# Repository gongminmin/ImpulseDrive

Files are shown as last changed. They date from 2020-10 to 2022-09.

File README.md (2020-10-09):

# Impulse Drive



In Star Trek universe, impulse drive is a propulsion system of spacecrafts for interplanetary travel. This project is trying to design a real-world impulse drive. The basic characteristics of this engine are

* Electric propulsion
* Large thrust
* Long specific impulse
* No or little moving parts
* Good scalability
* Low cost

We'd like to make it easy to implement, so people can build it as a hobby project.

NOTE: Please turn on git LFS when cloning this project.

## Method

There are many different engine designs for spacecraft propulsion, check [wikipedia](https://en.wikipedia.org/wiki/Spacecraft_propulsion#Table_of_methods) for a list. The only one design among them that fits these requirements is magnetoplasmadynamic thruster, a.k.a, MPDT or MPD thruster. More details in [MPD](Doc/Mpd.md).

Our design is based on MPDT, with several significant improvements.

## Design

The principle of our design, and a detailed introduction of modules are in [Design](Doc/Design.md)

## Disclaimer

MPD thruster is operated by **LETHALLY** high voltage and current. If you don't have enough knowledge and experiences on high voltage electric, please keep extreme cautions on insulation.

## Directories

* Circuit folder is the electric design of the system. The files can be open by [KiCad](https://kicad-pcb.org/)
* 3DModel folder is the 3D model design of some components. It's in [Blender](https://www.blender.org/) format.
* Doc folder contains some documents

## License

ImpulseDrive is distributed under the terms of MIT License. See [LICENSE](LICENSE) for details.

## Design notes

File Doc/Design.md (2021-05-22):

# Design

To make MPD thruster practical enough, we need to solve [drawbacks of MPD thruster](Mpd.md#Drawbacks).

## Improvements

### Power Source

To ionize the propellant, the power voltage needs to be very high. To generate large enough Lorentz force, the electric current need to be very high. However, a power source with both high voltage and high current is not practical.

To solve this, we borrow a concept from a welding machine. In its design, a starter provides 10kV high frequency AC to ionize some of the medium particles. An ion path is created from one electrode to another during the ionization phase. This path closes a low voltage capacitor bank circuit, which then pumps a high current to the medium to generate much more ion. One bonus is that AC is much easier to ionize medium than DC, it reduces the voltage requirement of the starter.

In this way, we need a power source to provide high voltage and low current, and a power source to provide high current and low voltage. The power requirement is reduced much.

### Parallel or Series

Now we have 2 power sources, one high voltage AC from starter and one high current DC from capacitor bank. But how to connect them together? We have 2 choices, parallel and series.

The first way is put starter and capacitor bank in parallel. However, to prevent the capacitor bank be damaged by the high voltage, and to prevent the starter to be damaged by the high current, they need some kinds of isolation.

One straight forward thought is put a RC filter or LC filter between capacitor bank and the nozzle, and a unpolarized capacitor between starter and nozzle. DC can go through RC filter or LC filter, but AC is blocked. Meanwhile AC can go through the unpolarized capacitor, but DC is blocked.

However, RC filter doesn't work for our scenario, because it limits the DC current from capacitor bank. LC filter is OK, but to survive under high current, the inductor must be a huge one. It'll become super expensive and super heavy.

The other choice is connecting them in series. There are 2 issues to do this. First, the high current needs to go through starter. Second, the high AC can damage polarized capacitors.

To solve the first issue, we need an isolation transformer. The primary coil is wrapped by thin wire, and secondary coil is wrapped by very thick wire. They have same turns. In this way, the voltage from primary side can be transformed to secondary coil with the same voltage. Meanwhile high current can go through its secondary coil without damaging the coil or starter.

The nature of the second issue is because AC keeps changing its direction, but polarized capacitor can't handle voltage with an inverted direction. It's not actually a problem. The voltage in the capacitor bank acts as a bias to the AC. Or, the AC doesn't charge the capacitor bank.

### Propellant

Xenon, neon, argon, and lithium have low ionization energies (see also [this table](https://en.wikipedia.org/wiki/Molar_ionization_energies_of_the_elements)). Lithium powder has higher density than gaseous propellants. This makes lithium become the best choice. However, these materials are expensive, and need special storage tank.

How about nitrogen? It's 1st, 2nd, and 3rd molar ionization energy are similar to argon's (Well, much higher ionization energy for 4th and 5th molar ionization energy). And nitrogen is super cheap, very easy to acquire. It also makes MPD thruster air-breathing.

(An under developing engine called SABRE has a precooler to liquefy the air from intake, store in the tank. If using a similar design here, a nitrogen-based MPD thruster don't even need to refuel a propellant tank before taking off.)

### Pre-ionization

To overcome the high ionization energy, we need to utilize [hollow cathode effect](https://en.wikipedia.org/wiki/Hollow_cathode_effect) to reduce the break down voltage of propellant. It's a hollow conduit cathode, instead of a solid one. The propellant is injected to the conduit and pushed to the open-end.

### Cooling

The hollow conduit cathode also acts as a cooling system. When the cold propellant goes through the conduit, it cools down the cathode. Same conduit cooling system can be applied to anode as well.

### Continuous or Pulse

TODO

## Operation Cycle

The propulsion system is running in cycles. Each cycle takes steps below.

Subsystems

1. The power starts charging the capacitor bank,
1. When the capacitor bank is full, signals are sent to control subsystem,
1. Turn on the inject system to push propellant into the nozzle,
1. Turn on the starter to generate an ion path inside the nozzle,
1. The capacitor bank starts discharging, which generates much more ion,
1. Turn on the electromagnet for applying a magnetic field to push the ion particles out,
1. Finish discharging the capacitor bank, return to step 1.

## Subsystems

The system is composed of several subsystems.

### Power

The power subsystem converts 12V DC to low voltage high frequency AC. One for starter, and one for charging capacitor bank.

See also [Power Subsystem](PowerSubsystem.md)

### Control

The control subsystem collects the signals from other subsystems, then decides when to turn on starter, capacitor bank, propellant injector, or electromagnet.

See also [Control Subsystem](ControlSubsystem.md)

### Starter

The starter transformed the AC from low voltage to ~10kV to ionize the propellant. It's very similar to a spark gap Tesla coil.

See also [Starter Subsystem](StarterSubsystem.md)

### Capacitor Bank

The low voltage AC from power subsystem is transformed to high voltage DC, and charge a bunch of capacitors. It can be discharged in a very short time peroid to generate a high current.

See also [Capacitor Bank Subsystem](CapacitorBankSubsystem.md)

### Nozzle

The nozzle contains a hollow cathode, a large piece of anode, and a electromagnet around it.

See also [Nozzle](Nozzle.md)

### Propellant Injector

A air compressor injects the propellant (air) to the nozzle.

See also [Propellant Injector](PropellantInjector.md)

## References

* [Matthew Krolak's electric engine](http://www.myelectricengine.com/)
* [First Breakthrough for Future Air-Breathing Magneto-Plasma Propulsion Systems](https://arxiv.org/ftp/arxiv/papers/1609/1609.04054.pdf)

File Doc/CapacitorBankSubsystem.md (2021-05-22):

# Capacitor Bank Subsystem

As the name suggested, the capacitor bank store energy in multiple capacitors, and enable to discharge all energy into the nozzle in a very short time period. This subsystem is separated into 2 modules.

## Adapter

The adapter module has 3 parts. The major part is a voltage converter. In the full capacitor bank, a transformer T1 is connected to ZVS driver in power subsystem. It transforms 18V AC to 300V. Then a 1-stage full-wave Cockcroft–Walton generator bring the voltage up to 840V DC (`3 * peak voltage = 3 * 198 * sqrt(2) = 840`). T1 is a homemade transformer based on EE42 core. Its primary coil is 6 turns with 24 AWG magnet wire, with ~27uH inductance. And its secondary coil is 50+50 turns with 32 AWG magnet wire. The outputs are used to charge and discharge the capacitor bank.

The next part is a voltage sensing circuit. It takes a low voltage signal from linear divider, compare it with reference voltages. During the charging, LEDs will be lit up one by one. If the capacitor bank is full, the 4th LED is on, and an isolated signal is sent out to control subsystem. The voltage sensing circuit needs a power source, so we need a auxilliary coil on the transformer T1 to get a 18V AC. It's then rectified and regulated to a 12V DC.

Adapter Circuit

## Capacitor Bank

The second module is the capacitor bank itself. The core component is 4 capacitors for welding machine, 330uF at 450V. They are connected together to form a capacitor with 330uF at 900V. In charging phase, a small current from J1 and J2 charges these capacitors, it takes seconds to finish charging. In discharging phase, the energy stores in them are discharged to J3 and J4 in less than 10 milliseconds with a high current. Each capacitor has its own bleeder resistor.

Capacitor Bank Circuit

## Mini Version

The high voltage capacitors are expensive and dangerous. During the experiment, we first implement a mini version of this subsystem. It has a relatively low working voltage, 68V.

The mini version has a small transformer by wrapping 24 AWG magnet wire on a T130-26 toroid iron powered core. The primary and secondary turns are 16:10. A 2-stage half-wave Cockcroft–Walton generator brings the voltage up to ~68V DC. Also, it has a much simpler linear divider. The voltage se*nsing part is the same, except it's running on 12V battery, and it's implementated on a separated PCB.

The capacitors are the same 330uF, but their voltage ratings are 50V. They are installed on the adapter PCB.

Capacitor Bank Photo

Note that the PCB follows a earlier design, with quick discharger on the bottom left. They are removed, so these components are not soldered.

## Calculations

Let's calculate the output current amperes from this capacitor bank. The definition of Farad is:

`C = A * s / V`

where *C* is capacitance in farad, *A* is output current in ampere, *s* is discharging time in second, *V* is capacitor's voltage. From this equation, we can derive the equation of calculating the output current,

`A = C * V / s`

The capacitor bank has a capacitance of 330uF, at 848V, and the discharging time is between 4ms and 10ms. Here we take the average time 7ms. Put these numbers in, we have,

`A = 0.00033 * 848 / 0.007 = 40.0`

This capacitor bank's output current is 40.0A.

The discharge time via bleeder resistors can also be diverged from this equation.

`C = A * s / V`

`s = C * V / A`

`s = C * R`, because `R = V / A`

In the capacitor bank module, the bleeder R is 220KΩ, the discharging time is

`s = 0.00033 * 220,000 = 72.6`

, which is a little over 1 minute.

**CAUSION**: This equation assumes the discharging voltage is always in the capacitor's peak voltage. For reality, the voltage drops during the discharging process. It increases the discharging time. For safey reason, we need to multiply the time by **at least 10**. The status can be observed from LEDs on voltage sensing circuit.

With the same equation, we can estimate the capacitor bank's charging time. The ZVS module is about 60W when its input voltage is 12V. For this capacitor bank, the maximum charging current is 60W / 848V = 0.07A.

`s = C * V / A = 0.00033 * 848 / 0.07 = 4.0`

So, it takes at least 4 seconds to charge the capacitor bank.

The energy stores in the mini capacitor bank is:

`J = 0.5 * C * V * V = 0.5 * 0.00033 * 68 * 68 = 0.75 J`

Meanwhile, the one in full capacitor bank is:

`J = 0.5 * C * V * V = 0.5 * 0.00033 * 848 * 848 = 118.65 J`

**Status**: Small-scale board done, need experiments with other components, 50%.

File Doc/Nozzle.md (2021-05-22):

# Nozzle

Nozzle is the place where the ion particles are generated and accelerated. Unlike chemical rocket engines, we don't need to handle high pressure and high temperature.

There are 3 major components in the nozzle, anode, cathode, and a electromagnet coil.

## Anode

It's a 1-inch to 3/4-inch cooper coupling, with a stainless-steel clamp around it to secure the wires.

Anode

## Cathode

To maximize the hollow cathode effect, we need a long and thin metal tube. One choice is a ball pump needle. One end can connect to the tube from air pump. The open end is where the propellant comes out.

Cathode

**CAUSION**: Don't touch any electrode before capacitor bank finish discharging. The voltage and current are lethal.

## Electromagnet

The electromagnet is a low current coil. Build a coil from scratch takes time, so we bought a car air conditioner compressor clutch coil. Its size and magnetic intensity fit our scenario.

Electromagnet

## Case

All these components are installed into a case. Here is a 3D model of it. It can be contructed by 3D printing or cardboard.

Nozzle Case

This is a cardboard version of the assembled nozzle. The clear tube is a aquarium airline tube from the propellant injector to the nozzle.

Nozzle Case

## Circuit

Other than the nozzle itself, the electromagnet coils need high current to work. A low voltage capacitor bank is introduced here. It's charged from power module to 12V, and triggered by control model to discharge its energy to coils.

Nozzle Circuit

**Status**: Work-in-progress, 40%.

## Alternative Design

The huge and heavy electromagnet can be replaced by multiple small ones. With the same current, they can provide same magnet field with much lighter in weight.

A better design of the case can be more compact and more robust. But it must use 3D printing to construct.

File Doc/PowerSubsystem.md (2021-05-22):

# Power Subsystem

The power subsystem contains 4 modules, as the diagram below.

Power Subsystem

A main power source provides a high current 12V DC power. The current is dispatched in switch module to capacitor bank, starter, electromagnet coil, or propellant injector. Since capacitor bank and starter requires AC as input, we need to add ZVS drivers to invert the DC to AC.

## Main Power Source

The first module is a 12V DC power source. Currently an ATX power supply unit from an old computer is used. Along with a board to turn the power unit on and off. It's easy to find these pieces online. It'll be replaced by a 12V battery in the future.

PSU Photo

**Status**: Done.

## Switch Module

The DC from main power source needs to be separated into multiple channels. One to capacitor bank, one to starter, one to electromagnet coil, and one to propellant injector. The 1-4 pins of J1 controls which ones are on through these solid state relays (SSRs) on switch module. Note that currently the electromagnet coil switch is on it's own circuit. Here we just passthrough the signal. This module is basically a 3-channel SSR, using a MOSFET to do the switching.

Power Switch Circuit

Also, this circuit provides a 12V power to electromagnet coil, and a 5V power to control board. (This photo will be updated soon).

Power Switch Photo

**Status**: The old board works, needs to be updated, 50%.

## ZVS Driver

A ZVS driver is a circuit that can oscillate a large amount of DC power with very high efficiency. This design here is a well known one, invented by Vladimiro Mazzilli.

ZVS Circuit

It's also a finished board that can be found online. To make it oscillate, the output must be connected to a inductor, such as the primary coil of a transformer. Here we choose the inductance at 28uH, the output voltage is between 18 to 20V. The dual inductor ZVS driver doesn't need a center tapped primary coil. Make the circuit easier to connect.

ZVS Photo

**Status**: Done.

## Calculations

The resonant frequency of ZVS driver is detemined by its LC circuit.

`f = 1 / (2 * PI * sqrt(L * C))`

L is the primary coil of T1. It's measured as 28uH. And C here is 0.66uF. Put them into the equation, we have,

`f = 1 / (2 * PI * sqrt(0.000028 * 0.00000066)) = 37.0 kHz`

The impedance of the L is,

`X = 2 * PI * f * L = 2 * PI * 37000 * 0.000028 = 6.5 Ω`

**Status**: Done.

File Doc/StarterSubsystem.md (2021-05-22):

# Starter Subsystem

The starter subsystem is used to start an arc in the nozzle. The input is a low voltage AC, and outputs AC is around 10kV.

Starter Circuit

The circuit is basically a spark gap Tesla coil (SGTC). The capacitors are in parallel with the T1 and the spark gap is in series to the T2's primary coil. An alternative circuit configuration is exchanging the place of capacitors and spark gaps. But the configuration in the diagram above is more suitable for our high frequency AC power.

First, the low voltage AC is transformed to 10kV by a flyback transformer T1. It's a kind of transformer commonly used in high voltage projects. It can be salvaged from old CRT TV, or laser printer. Note that most flyback transformer later than 1990s contains a diode inside, or even a one stage Cockcroft–Walton generator to multiply the voltage. The output of a modern flyback transformer is pulse DC or constant DC, not AC.

Flyback Transformer

Then it charges capacitors. Here we take 2 high voltage **polypropylene** capacitor connected in series. The material is very important, it must be polypropylene.

When capacitors reach T1's peak output voltage, the voltage between spark gap electrodes is high enough to breakdown the gas inside, to generate a electric path. The spark gap here is a homemade component.

Spark Gap Parts

The white part is a PVC reducer bushing. Drill 2 holes on its sides, and install 2 screws as electrodes. On the tip of the screws, put a pull chain brass ball on each one. Knobs are used to secure the wires.

Spark Gap Assembled

When the spark gap is jumped, it closes the circuit and the capacitors and the primary coil of T2 become a LC resonator. A high frequency AC is generated, and then transformed to the secondary coil of T2.

T2 is a home made air-core transformers. It's primary coil is in 22 AWG, and its secondary coil is in 18 AWG or thicker to allow high current from capacitor bank to pass through.

Other components are for safeness. L1 and L2 are filtering out high frequency resonate from LC circuit damage T1. R1 and R2 are bleeder resistors for C1 and C2. R3 is limiting the induced current in the circuit.

This subsystem is still in experiment. The results are not good. The high voltage running on the PCB is very dangerous. It jumps in many places, creating noises and sparks. Moving forward to a safer and solid design is necessary.

**CAUSION**: Everything after the flyback transformer are in ~10kV. Keep distance with them even after shut this subsystem down. The capacitors may still charge. When operating, the spark gap can be loud and hot. Very careful about the metal parts.

**Status**: Experiment-in-progress, 30%.

## Calculations

The LC circuit is composed of C1 (10nF), C2, and the primary coil of T2 (5.7uH). The frequency is,

`f = 1 / (2 * PI * sqrt(L * C)) = 1 / (2 * PI * sqrt(Lt * C1 / 2)) = 1 / (2 * PI * sqrt(0.0000057 * 0.00000001 / 2)) = 943.2 kHz`

The impedance of the L is,

`X = 2 * PI * f * L = 2 * PI * 943200 * 0.0000057 = 33.8 Ω`

## Alternative Design

Due to the spark gap, this module is very noisy, and looks dangerous. An improvement is borrowing the design of a solid-state Tesla coil (SSTC), dual resonant solid-state Tesla coil (DRSSTC) to be exact.

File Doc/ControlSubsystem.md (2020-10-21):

# Control Subsystem

The control subsystem behaves as a logic circuit. It's triggered by a fully charged signal from capacitor bank. Then signals are sent out to turn on or off other subsystems. The timing diagram looks like this.

Control Output Timing Diagram

This image is generated by [WaveDrom](https://wavedrom.com).
<details>
  <summary>Click to see the code.</summary>
  <pre>
{
  signal: [
    {name: 'Trigger', wave: 'h..Nh........'},
    {},
    {name: 'Electromagnet', wave: 'l.......h.l..', node: '...a....b.c'},
    {name: 'Starter', wave: 'l.......h.l..'},
    {name: 'Propellant Injector', wave: 'l..h.l.......', node: '...d.e'},
    {name: 'Capacitor Bank', wave: 'h.......l.h..'}
  ],
  edge: [
    'd<->e t1', 'a<->b t2', 'b<->c t3'
  ]
}</pre>
</details>

When the trigger signal is in its falling edge, a high logic signal lasts for **t1** turns on the propellant injector. After **t2**, electromagnet and starter are turned on by a same high logic signal lasts for **t3**. The capacitor signal is inverse of coil or starter signal. The delay between propellant injector and starter is because the propellant needs some time to reach the nozzle.

Control Circuit

Three NE555 monostable circuit are used in the control subsystem. When the input signal comes in, it triggers U1 and U3 at the same time. U3 outputs the propellant injector signal, where RV3 controls **t1**. U1 outputs a intermediate signal to U2, where RV1 controls the delay **t2**. Finally, U2 is triggered by the falling edge of U1's output. It then sends out the coil and starter signal, where RV2 controls **t3**. The signal is inverted by Q1 to form the capacitor signal.

Control Photo

**Status**: Done.

## Alternative Design

This circuit can be implemented by a ATtiny85 or Arduino with the code to run the logic.

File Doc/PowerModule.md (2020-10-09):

# Power Module

The power module contains 3 parts. They'll be explained below.

## DC Power Source

The first part is a 12V DC power source. Currently an ATX power supply unit from an old computer is used. Along with a board to turn the power unit on and off. It's easy to find these pieces online. It'll be replaced by a 12V battery in the future.

PSU Photo

**Status**: Done.

## ZVS Driver

A ZVS driver is a circuit that can oscillate a large amount of DC power with very high efficiency. This design here is a well known one, invented by Vladimiro Mazzilli.

ZVS Circuit

It's also a finished board that can be found online. The output of this board is connected to a 5+5:10 homemade toroid transformer. It doesn't change the voltage, but isolate the two sides. On the primary coil side, the ZVS can keep oscillating. Meanwhile on the secondary coil side, it pumps the power to the successor circuit. The transformer is made from a FT240-61 ferrite core. Each of its coil has a inductance of 27uH.

ZVS Photo

**Status**: Done.

## Power Switch

The DC from power source and AC from ZVS driver are separated into multiple channels. One to capacitor bank, one to starter, and one to electromagnet coil. When the ControlSignal is low level, the capacitor bank channel is on, other two ones are switched off.

Power Switch Circuit

Since the output to starter and capacitor bank are AC, a regular triac-based solid state relay also doesn't work here. Triac is not able to be turned off by cut off the signal. Instead, here we use 2 MOSFETs connected back-to-back to act as an AC solid state switch. The output to electromagnet coil is DC, just one MOSFET is enough.

The circuit is hand soldered on a prototyping board.

Power Switch Photo

## Calculations

The resonant frequency of ZVS driver is detemined by its LC circuit.

`f = 1 / (2 * PI * sqrt(L * C))`

L is the primary coil of T1. It's measured as 27uH. And C here is 0.66uF. Put them into the equation, we have,

`f = 1 / (2 * PI * sqrt(0.000027 * 0.00000066)) = 37.7 kHz`

The impedance of the L is,

`X = 2 * PI * f * L = 2 * PI * 37700 * 0.000027 = 6.39 Ω`

**Status**: Done.

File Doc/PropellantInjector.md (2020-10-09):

# Propellant Injector

Currently we are using air as the propellant. So, the injector is just an air compressor or pump. Here a cheap fish tank air pump is used for this purpose. It takes 120V AC electric supply, and it's always on. In the future, it'll be modified to take a DC 12V power source, and switched by control subsystem.

Propellant Injector Photo

**Status**: Done.

## Alternative Design

Another solution is taking a liquid nitrogen tank as the gas source, and have a controllable switch to turn it on and off.

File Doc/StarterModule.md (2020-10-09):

# Starter Module

The starter module is used to start an arc in the nozzle. The input is 12V AC, and outputs pulsed DC at around 10kV.

Starter Circuit

The circuit is basically a spark gap Tesla coil (SGTC). The capacitors are in parallel with the T1 and the spark gap is in series to the T2's primary coil. An alternative circuit configuration is exchanging the place of capacitors and spark gaps. But the configuration in the diagram above is more suitable for our high frequency AC power.

First, the 12V AC is transformed to 10kV by a flyback transformer T1. It's a kind of transformer commonly used in high voltage projects. It can be salvaged from old CRT TV, or laser printer. Note that most flyback transformer later than 1990s contains a diode inside, or even a one stage Cockcroft–Walton generator to multiply the voltage. The output of a modern flyback transformer is pulse DC or constant DC, not AC.

Flyback Transformer

Then it charges capacitors. Here we take 2 high voltage **polypropylene** capacitor connected in series. The material is very important, it must be polypropylene.

When capacitors reach T1's peak output voltage, the voltage between spark gap electrodes is high enough to breakdown the gas inside, to generate a electric path. The spark gap here is a homemade component.

Spark Gap Parts

The white part is a PVC reducer bushing. Drill 2 holes on its sides, and install 2 screws as electrodes. On the tip of the screws, put a pull chain brass ball on each one. Knobs are used to secure the wires.

Spark Gap Assembled

When the spark gap is jumped, it closes the circuit and the capacitors and the primary coil of T2 become a LC resonator. A high frequency AC is generated, and then transformed to the secondary coil of T2.

In the next step, the output of T2's secondary coil is rectified to pulsed DC, and transformed by T3 to the output ends. **QUESTION**: Can D1 and D2 hold the current?

T2's primary and secondary coils have same wire gauge, AWG 22. T3's primary coil is in AWG 22, and its secondary coil is in AWG 18 or thicker to allow high current from capacitor bank to pass through.

Other components are for safeness. L1 and L2 are filtering out high frequency resonate from LC circuit damage T1. R1 and R2 are bleeder resistors for C1 and C2. R3 and R4 are limiting the induced current in the circuit.

This module is still in experiment. Need more time to finish it.

TODO: Assembled module photo

**CAUSION**: Everything after the flyback transformer are in ~10kV. Keep distance with them even after shut this module down. The capacitors may still charge. When operating, the spark gap can be loud and hot. Very careful about the metal parts.

**Status**: Experiment-in-progress, 30%.

Due to the spark gap, this module is very noisy, and looks dangerous. An improvement is borrowing the design of a solid-state Tesla coil (SSTC), dual resonant solid-state Tesla coil (DRSSTC) to be exact.

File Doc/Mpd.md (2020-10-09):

# Magnetoplasmadynamic Thruster

A MPD thruster is an electric propulsion without moving parts. It could produce 100N level of thrust, much larger than ion thruster (0.1N), arcjet (<10N), pulsed plasma thruster (0.1N), etc. The specific impulse and exhaust velocity are extremely high.

## Principle

Lorentz force provides the thrust for a MPD thruster. Generally, a gaseous propellant is ionized by a **extreme voltage** power source. The ion flow is fed into an acceleration chamber, where the magnetic and electrical fields are created using a **high current** power source. The particles are then propelled by the Lorentz force resulting from the interaction between the current flowing through the plasma and the magnetic field out through the exhaust chamber.

There are two main types of MPD thrusters, applied-field and self-field. Applied-field thrusters have magnetic rings surrounding the exhaust chamber to produce the magnetic field, while self-field thrusters have a cathode extending through the middle of the chamber. Applied fields are necessary at lower power levels (<100kW>), where self-field configurations are too weak.

Due to the power level limitation, we focus on applied fields MPD thruster.

## Drawbacks

Of course, MPD thruster is not perfect. To make it pratical, we need to confront its drawbacks.

* Super high watts power source. For ionize propellant, extreme voltage is required. For generats high Lorentz force, high current is required. If naivelly takes one power source to provide both extreme voltage and high current, it sounds bad. you don't have a nuclear power, right?

* Propellant to use. A good propellant for MPD needs to have a low ionization energy and high mass. Various propellants such as xenon, neon, argon, and lithium have been used, with lithium generally being the best performer. However, these propellants are expensive.

* Electrode erosion. High current arc damages the electrode. It dramatically reduces the lifespan of nozzle.

## References

* [A lecture of MPD from MIT](https://ocw.mit.edu/courses/aeronautics-and-astronautics/16-522-space-propulsion-spring-2015/lecture-notes/MIT16_522S15_Lecture19.pdf)
* [Lorentz Force Accelerators from Princeton](https://alfven.princeton.edu/research/lfa)
* [Matthew Krolak's electric engine](http://www.myelectricengine.com/)

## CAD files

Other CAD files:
3DModel/Nozzle/Coil.blend
3DModel/Nozzle/NozzleAnode.blend
3DModel/Nozzle/NozzleCase-PVC.blend
3DModel/Nozzle/NozzleCase.blend
3DModel/Nozzle/NozzleCathode.blend

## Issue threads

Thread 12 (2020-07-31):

Build power switch board

gongminmin, 2020-07-31:

gongminmin, 2020-08-04:
Need a major redesign.

Closed 2020-08-11.

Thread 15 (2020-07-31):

Build starter output board

gongminmin, 2020-07-31:

gongminmin, 2020-09-06:
Merge to issue #17

Closed 2020-09-06.

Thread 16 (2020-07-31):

Test starter output board

gongminmin, 2020-07-31:
Use 12V AC and switch board tester to test the starter output board.

gongminmin, 2020-08-28:
Tested on bread board.

Closed 2020-08-28.

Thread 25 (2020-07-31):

Test system with simplified mini capacitor bank

gongminmin, 2020-07-31:
10kV 3.2A

gongminmin, 2020-09-06:
Merged to issue #23

Closed 2020-09-06.

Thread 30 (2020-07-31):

Simplify control board to 1 channel

gongminmin, 2020-07-31:

gongminmin, 2020-10-14:
Redesigned the board. Need to rebuild it.

Closed 2020-10-19.

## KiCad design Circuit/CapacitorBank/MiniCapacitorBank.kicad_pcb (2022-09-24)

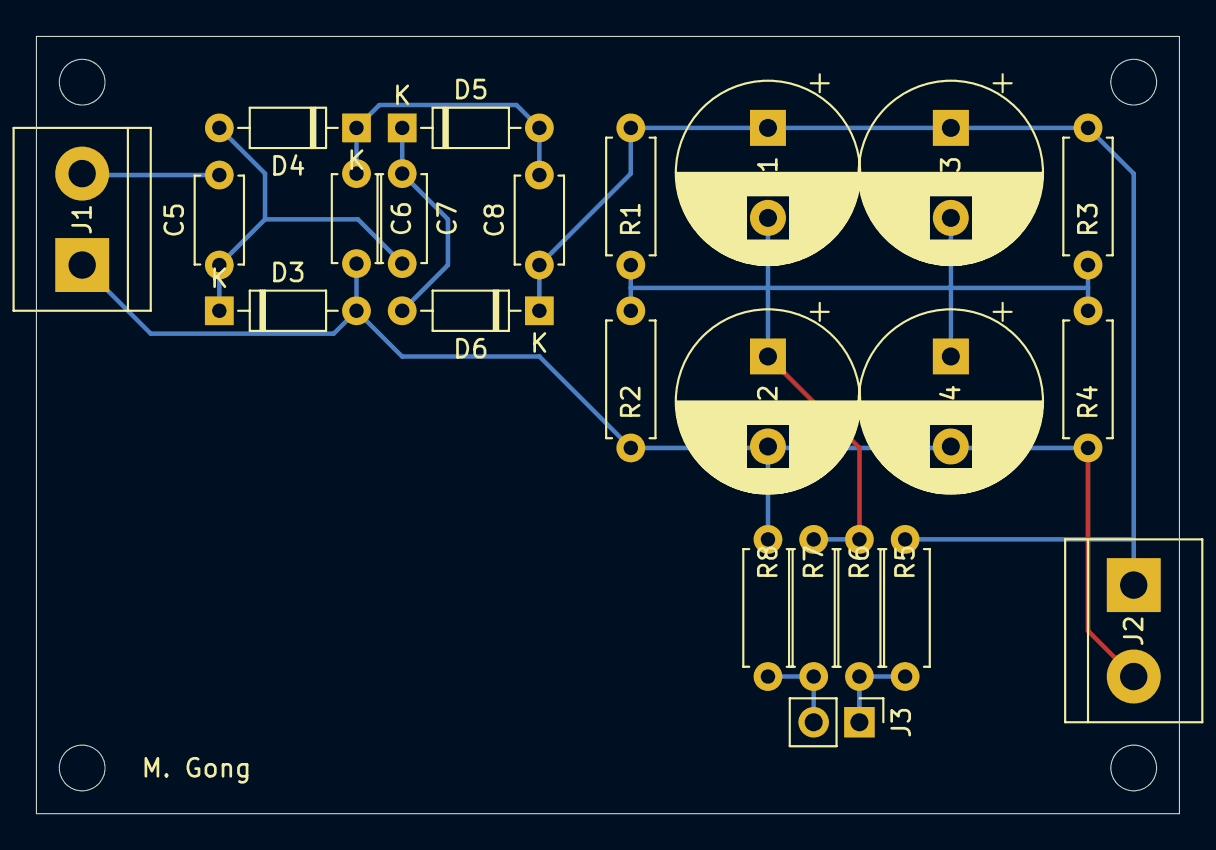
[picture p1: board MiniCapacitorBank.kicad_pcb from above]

Board: 2 copper layers, 63.5 x 43.2 mm, 23 parts (0 on the bottom side), 9 nets.

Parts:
C1, C2, C3, C4: 330uF/50V; CP_Radial_D10.0mm_P5.00mm
C5, C6, C7, C8: 0.1uF; C_Disc_D4.7mm_W2.5mm_P5.00mm
D3, D4, D5, D6: 1N4148; D_DO-35_SOD27_P7.62mm_Horizontal
J1: AC Power In; TerminalBlock_bornier-2_P5.08mm
J2: 68V out; TerminalBlock_bornier-2_P5.08mm
J3: To Voltage Sensing; PinHeader_1x02_P2.54mm_Vertical
R1, R2, R3, R4: 68K; R_Axial_DIN0207_L6.3mm_D2.5mm_P7.62mm_Horizontal
R5, R8: 1M; R_Axial_DIN0207_L6.3mm_D2.5mm_P7.62mm_Horizontal
R6, R7: 100K; R_Axial_DIN0207_L6.3mm_D2.5mm_P7.62mm_Horizontal

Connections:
/ACPowerIn+: C5.2, J1.2
/ACPowerIn-: C2.2, C4.2, C6.2, D3.2, J1.1, J2.2, R2.2, R4.2, R8.2
/PowerOut+: C1.1, C3.1, C8.1, D6.1, J2.1, R1.1, R3.1, R5.1
/Sensor0V: J3.2, R7.2, R8.1
/Sensor6V: J3.1, R5.2, R6.1
unnamed: C1.2, C2.1, C3.2, C4.1, R1.2, R2.1, R3.2, R4.1, R6.2, R7.1
unnamed: C5.1, C7.2, D3.1, D4.2
unnamed: C6.1, C8.2, D4.1, D5.2
unnamed: C7.1, D5.1, D6.2

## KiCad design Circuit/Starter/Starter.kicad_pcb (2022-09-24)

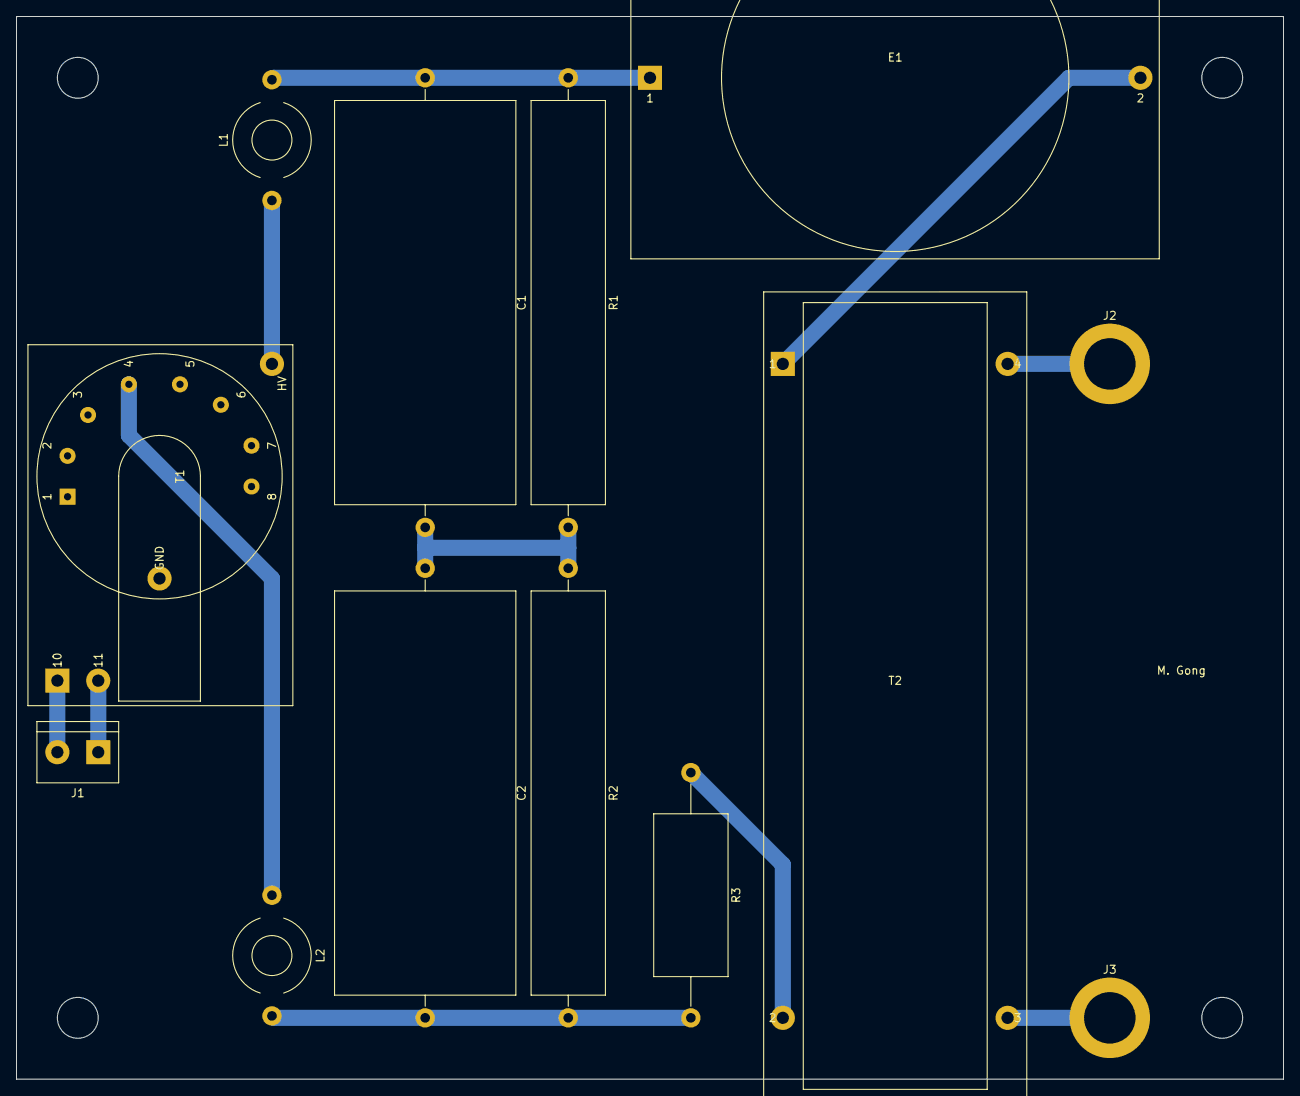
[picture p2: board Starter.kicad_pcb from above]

Board: 2 copper layers, 157.5 x 132.1 mm, 13 parts (0 on the bottom side), 11 nets.

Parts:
C1, C2: 10nF/8kV; C_Axial_L50.0mm_D23.0mm_P55.0mm_Horizontal
E1: SPARK_GAP 10kV; Spark_Gap
J1: From Power; TerminalBlock_bornier-2_P5.08mm
J2: Output+; MountingHole_6.4mm_M6_ISO14580_Pad
J3: Output-; MountingHole_6.4mm_M6_ISO14580_Pad
L1, L2: 10uH; L_Toroid_Horizontal_D9.5mm_P15.00mm_Diameter10-5mm_Amidon-T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
R1, R2: 100M/5W; R_Axial_Power_L50.0mm_W9.0mm_P55.88mm
R3: 1Ω/10W; R_Axial_DIN0922_L20.0mm_D9.0mm_P30.48mm_Horizontal
T1: BSH12-N406L 8:6400; Flyback_Transformer_BSH12-N406L
T2: 20:20; Air_Core_Transformer_1P_1S

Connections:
/PowerIn+: J1.2, T1.10
/PowerIn-: J1.1, T1.11
/PowerOut+: J2.1, T2.4
/PowerOut-: J3.1, T2.3
unnamed: C1.1, E1.1, L1.2, R1.1
unnamed: C1.2, C2.1, R1.2, R2.1
unnamed: C2.2, L2.2, R2.2, R3.2
unnamed: E1.2, T2.1
unnamed: L1.1, T1.12
unnamed: L2.1, T1.4
unnamed: R3.1, T2.2

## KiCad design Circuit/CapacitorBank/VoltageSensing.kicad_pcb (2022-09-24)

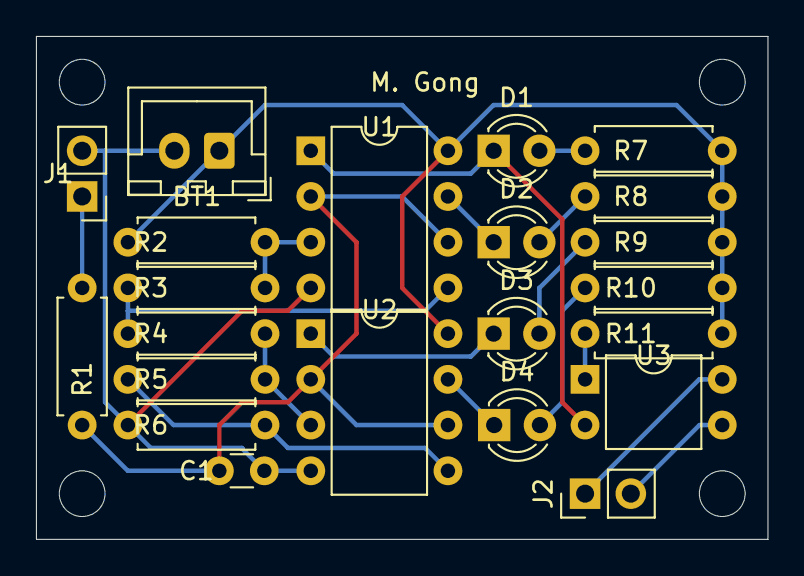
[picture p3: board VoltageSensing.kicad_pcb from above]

Board: 2 copper layers, 40.6 x 27.9 mm, 22 parts (0 on the bottom side), 19 nets.

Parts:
BT1: 12V Battery; JST_XH_B2B-XH-A_1x02_P2.50mm_Vertical
C1: 0.1uF; C_Disc_D3.0mm_W1.6mm_P2.50mm
D1, D2, D3, D4: LED; LED_D3.0mm_FlatTop
J1: From Capacitor Bank; PinHeader_1x02_P2.54mm_Vertical
J2: To Control; PinHeader_1x02_P2.54mm_Vertical
R1, R11: 1K; R_Axial_DIN0207_L6.3mm_D2.5mm_P7.62mm_Horizontal
R2: 20K; R_Axial_DIN0207_L6.3mm_D2.5mm_P7.62mm_Horizontal
R3, R4, R5, R6: 4.7K; R_Axial_DIN0207_L6.3mm_D2.5mm_P7.62mm_Horizontal
R7, R8, R9, R10: 2.2K; R_Axial_DIN0207_L6.3mm_D2.5mm_P7.62mm_Horizontal
U1, U2: LM393; DIP-8_W7.62mm
U3: PC817; DIP-4_W7.62mm

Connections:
+12V: BT1.1, R2.2, R7.1, R8.1, R9.1, R10.1, R11.1, U1.8, U2.8
/ControlGND: J2.2, U3.3
/ControlSignal: J2.1, U3.4
/Sensor6V: J1.1, R1.2
GND: BT1.2, C1.2, J1.2, R6.1, U1.4, U2.4
unnamed: C1.1, R1.1, U1.2, U1.6, U2.2, U2.6
unnamed: D1.1, U1.1, U3.2
unnamed: D1.2, R7.2
unnamed: D2.1, U1.7
unnamed: D2.2, R8.2
unnamed: D3.1, U2.1
unnamed: D3.2, R9.2
unnamed: D4.1, U2.7
unnamed: D4.2, R10.2
unnamed: R2.1, R3.2, U1.3
unnamed: R3.1, R4.2, U1.5
unnamed: R4.1, R5.2, U2.3
unnamed: R5.1, R6.2, U2.5
unnamed: R11.2, U3.1

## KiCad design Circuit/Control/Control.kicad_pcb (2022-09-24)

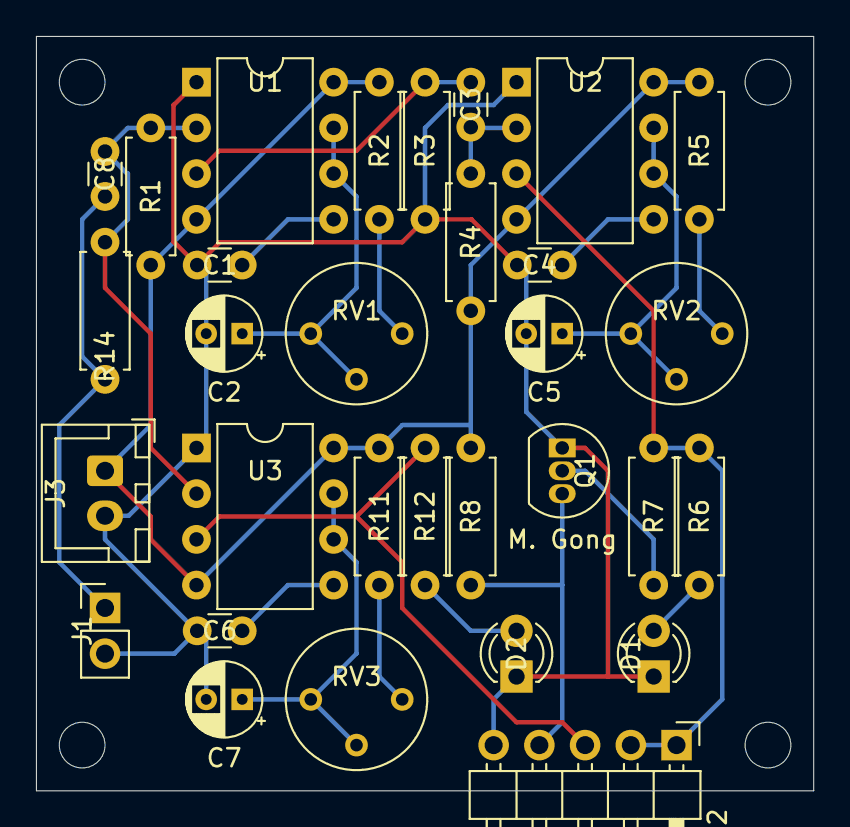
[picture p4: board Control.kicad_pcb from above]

Board: 2 copper layers, 43.2 x 41.9 mm, 31 parts (0 on the bottom side), 21 nets.

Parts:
C1, C3, C4, C6, C8: 0.01uF; C_Disc_D3.0mm_W1.6mm_P2.50mm
C2, C5, C7: 1uF; CP_Radial_D4.0mm_P2.00mm
D1, D2: LED; LED_D3.0mm_FlatTop
J1: Signal; PinHeader_1x02_P2.54mm_Vertical
J2: To Switch; PinHeader_1x05_P2.54mm_Horizontal
J3: Power; JST_XH_B2B-XH-A_1x02_P2.50mm_Vertical
Q1: 2N3904; TO-92_Inline
R1, R4, R7: 3.3K; R_Axial_DIN0207_L6.3mm_D2.5mm_P7.62mm_Horizontal
R2, R5, R11: 2K; R_Axial_DIN0207_L6.3mm_D2.5mm_P7.62mm_Horizontal
R3, R14: 4.7K; R_Axial_DIN0207_L6.3mm_D2.5mm_P7.62mm_Horizontal
R6, R8, R12: 1K; R_Axial_DIN0207_L6.3mm_D2.5mm_P7.62mm_Horizontal
RV1, RV2, RV3: 50K; Potentiometer_Bourns_3339P_Vertical
U1, U2, U3: NE555; DIP-8_W7.62mm

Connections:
+5V: J3.1, R1.1, R2.1, R4.1, R5.1, R8.1, R11.1, U1.4, U1.8, U2.4, U2.8, U3.4, U3.8
/CapacitorSignal: J2.4, Q1.3, R8.2
/CoilSignal: J2.1, J2.2, R6.1, R7.1, U2.3
/InjectorSignal: J2.3, R12.1, U3.3
/VoltageSensingSignal: C8.1, J1.1, R14.2
GND: C1.2, C2.2, C4.2, C5.2, C6.2, C7.2, D1.1, D2.1, J1.2, J2.5, J3.2, Q1.1, R3.2, U1.1, U2.1, U3.1
unnamed: C1.1, U1.5
unnamed: C2.1, RV1.2, RV1.3, U1.6, U1.7
unnamed: C3.1, R3.1, U1.3
unnamed: C3.2, R4.2, U2.2
unnamed: C4.1, U2.5
unnamed: C5.1, RV2.2, RV2.3, U2.6, U2.7
unnamed: C6.1, U3.5
unnamed: C7.1, RV3.2, RV3.3, U3.6, U3.7
unnamed: C8.2, R1.2, R14.1, U1.2, U3.2
unnamed: D1.2, R6.2
unnamed: D2.2, R12.2
unnamed: Q1.2, R7.2
unnamed: R2.2, RV1.1
unnamed: R5.2, RV2.1
unnamed: R11.2, RV3.1

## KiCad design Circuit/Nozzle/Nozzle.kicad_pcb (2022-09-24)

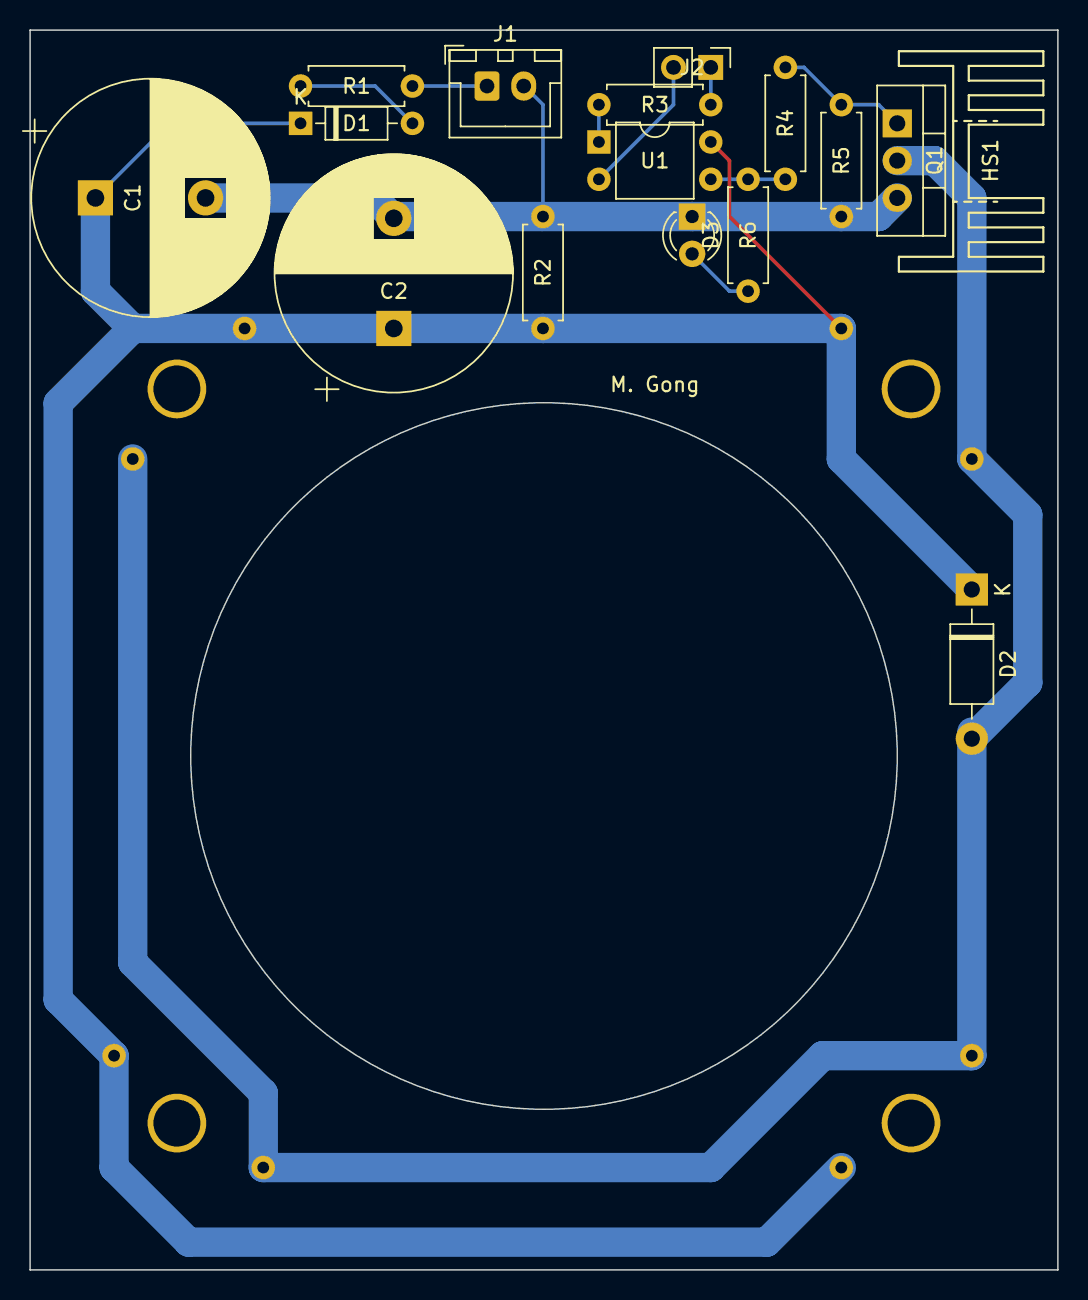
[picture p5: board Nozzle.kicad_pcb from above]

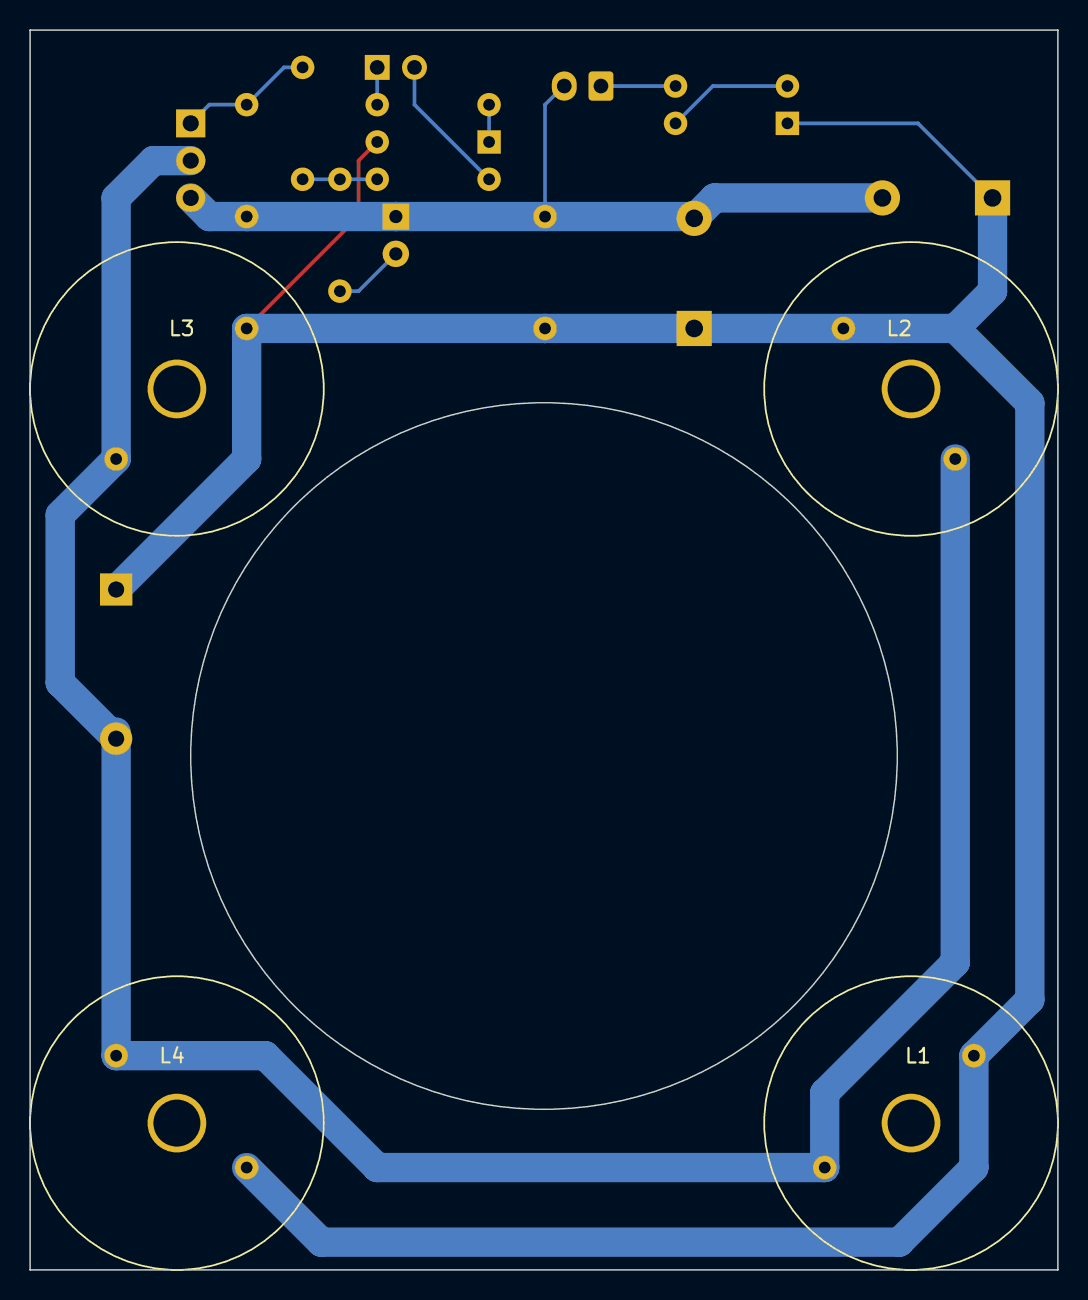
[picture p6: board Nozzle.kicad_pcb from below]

Board: 2 copper layers, 70.0 x 84.4 mm, 20 parts (4 on the bottom side), 11 nets.

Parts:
C1, C2: 4700uF; CP_Radial_D16.0mm_P7.50mm
D1: 1N4148; D_DO-35_SOD27_P7.62mm_Horizontal
D2: 1N4007; D_DO-41_SOD81_P10.16mm_Horizontal
D3: LED; LED_D3.0mm_FlatTop
HS1: Heatsink; Heatsink_TO220_15x10mm
J1: Coil Power; JST_XH_B2B-XH-A_1x02_P2.50mm_Vertical
J2: CoilSignal; PinHeader_1x02_P2.54mm_Vertical
L1, L2, L3, L4: Electromagnetic; Electromagnet
Q1: RFP30N06LE; TO-220-3_Vertical
R1: 220; R_Axial_DIN0207_L6.3mm_D2.5mm_P7.62mm_Horizontal
R2: 5.1K; R_Axial_DIN0207_L6.3mm_D2.5mm_P7.62mm_Horizontal
R3: 680; R_Axial_DIN0207_L6.3mm_D2.5mm_P7.62mm_Horizontal
R4: 4.7K; R_Axial_DIN0207_L6.3mm_D2.5mm_P7.62mm_Horizontal
R5: 10K; R_Axial_DIN0207_L6.3mm_D2.5mm_P7.62mm_Horizontal
R6: 2.2K; R_Axial_DIN0207_L6.3mm_D2.5mm_P7.62mm_Horizontal
U1: PC817; DIP-4_W7.62mm

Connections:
/CoilPower+: J1.1, R1.2
/CoilPower-: C1.2, C2.2, D3.1, J1.2, Q1.3, R2.2, R5.2
/CoilSignal+: J2.1, R3.2
/CoilSignal-: J2.2, U1.2
unnamed: C1.1, C2.1, D1.1, D2.1, L1.1, L2.1, L3.1, L4.1, R2.1, U1.4
unnamed: D1.2, R1.1
unnamed: D2.2, L1.2, L2.2, L3.2, L4.2, Q1.2
unnamed: D3.2, R6.2
unnamed: Q1.1, R4.1, R5.1
unnamed: R3.1, U1.1
unnamed: R4.2, R6.1, U1.3

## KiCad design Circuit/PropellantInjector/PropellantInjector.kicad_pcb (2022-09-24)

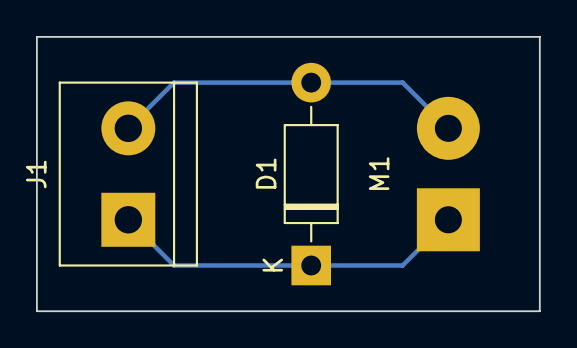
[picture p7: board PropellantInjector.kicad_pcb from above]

Board: 2 copper layers, 27.9 x 15.2 mm, 3 parts (0 on the bottom side), 2 nets.

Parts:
D1: 1N4007; D_DO-41_SOD81_P10.16mm_Horizontal
J1: Injector Power; TerminalBlock_bornier-2_P5.08mm
M1: Motor_DC; SolderWirePad_1x02_P5.08mm_Drill1.5mm

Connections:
/InjectorPower+: D1.1, J1.1, M1.1
/InjectorPower-: D1.2, J1.2, M1.2

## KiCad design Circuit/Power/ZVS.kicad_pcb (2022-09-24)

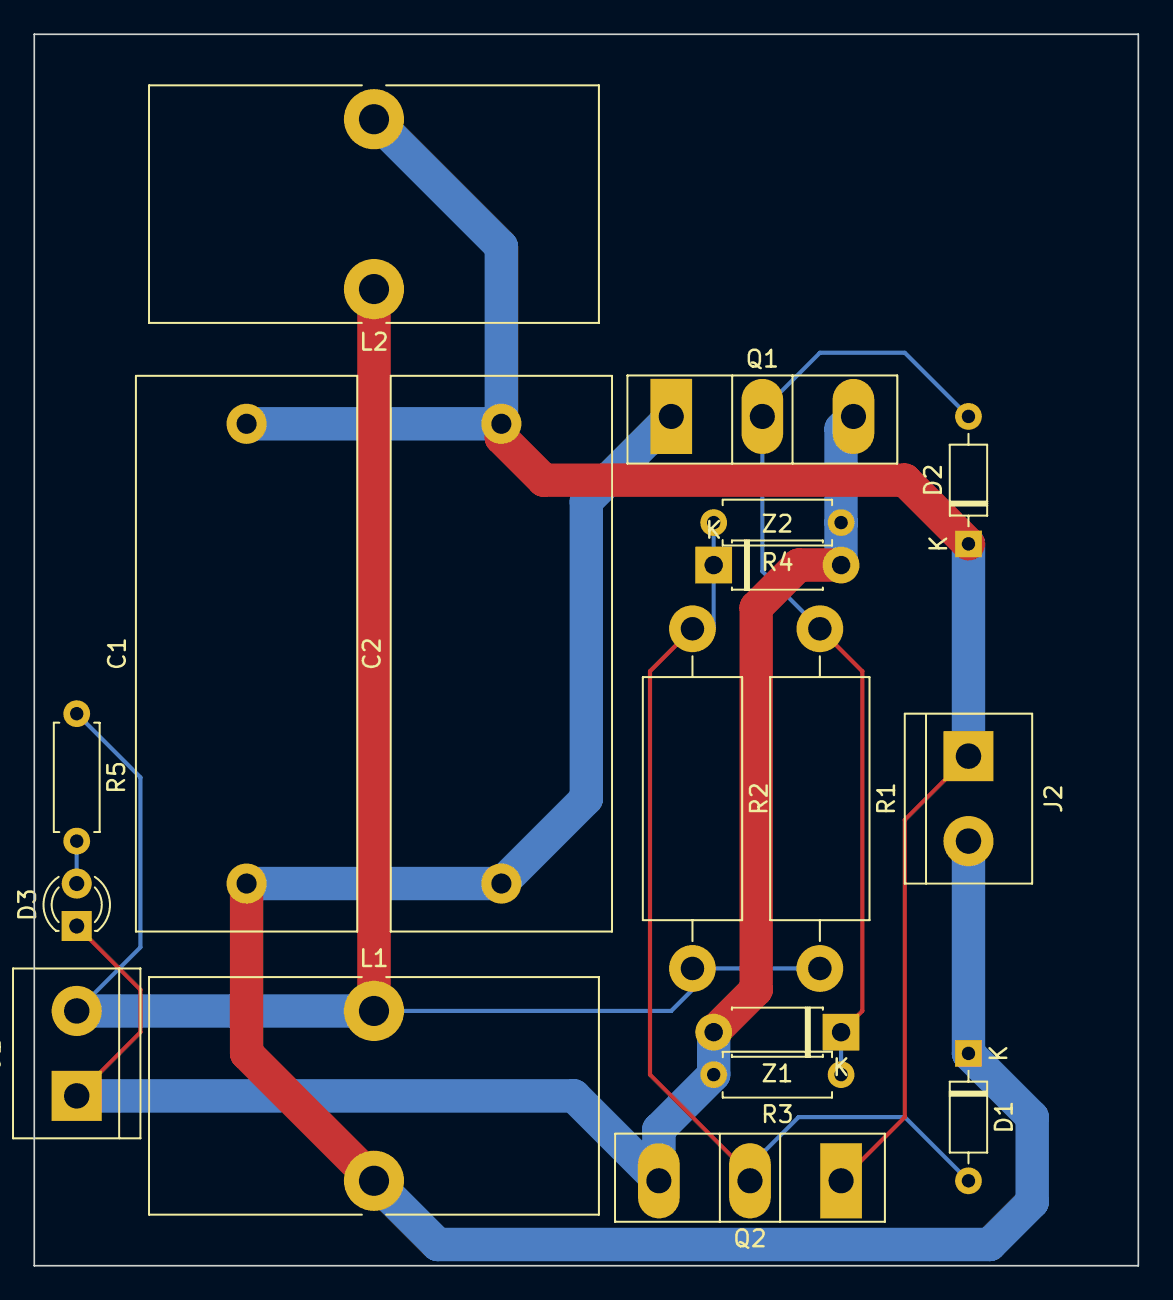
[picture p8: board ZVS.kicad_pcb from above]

Board: 2 copper layers, 66.0 x 73.7 mm, 18 parts (0 on the bottom side), 7 nets.

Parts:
C1, C2: MKP 0.33uF; C_Rect_L33.0mm_W13.0mm_P27.50mm_MKS4
D1, D2: FR107; D_DO-35_SOD27_P7.62mm_Horizontal
D3: LED; LED_D3.0mm_FlatTop
J1: 12V DC in; TerminalBlock_bornier-2_P5.08mm
J2: Output; TerminalBlock_bornier-2_P5.08mm
L1, L2: 100uH; L_Toroid_Vertical_L26.7mm_W14.0mm_P10.16mm_Pulse_D
Q1, Q2: IRFP250; TO-247-3_Vertical
R1, R2: 470 2W; R_Axial_DIN0614_L14.3mm_D5.7mm_P20.32mm_Horizontal
R3, R4: 10K; R_Axial_DIN0207_L6.3mm_D2.5mm_P7.62mm_Horizontal
R5: 2.2K; R_Axial_DIN0207_L6.3mm_D2.5mm_P7.62mm_Horizontal
Z1, Z2: 1N4742; D_DO-41_SOD81_P7.62mm_Horizontal

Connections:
/DCInput+: J1.2, L1.1, L2.1, R1.2, R2.2, R5.1
/DCInput-: D3.1, J1.1, Q1.3, Q2.3, R3.2, R4.1, Z1.2, Z2.2
/Output+: C1.1, C2.1, D1.1, J2.2, L1.2, Q1.1
/Output-: C1.2, C2.2, D2.1, J2.1, L2.2, Q2.1
unnamed: D1.2, Q2.2, R2.1, R4.2, Z2.1
unnamed: D2.2, Q1.2, R1.1, R3.1, Z1.1
unnamed: D3.2, R5.2

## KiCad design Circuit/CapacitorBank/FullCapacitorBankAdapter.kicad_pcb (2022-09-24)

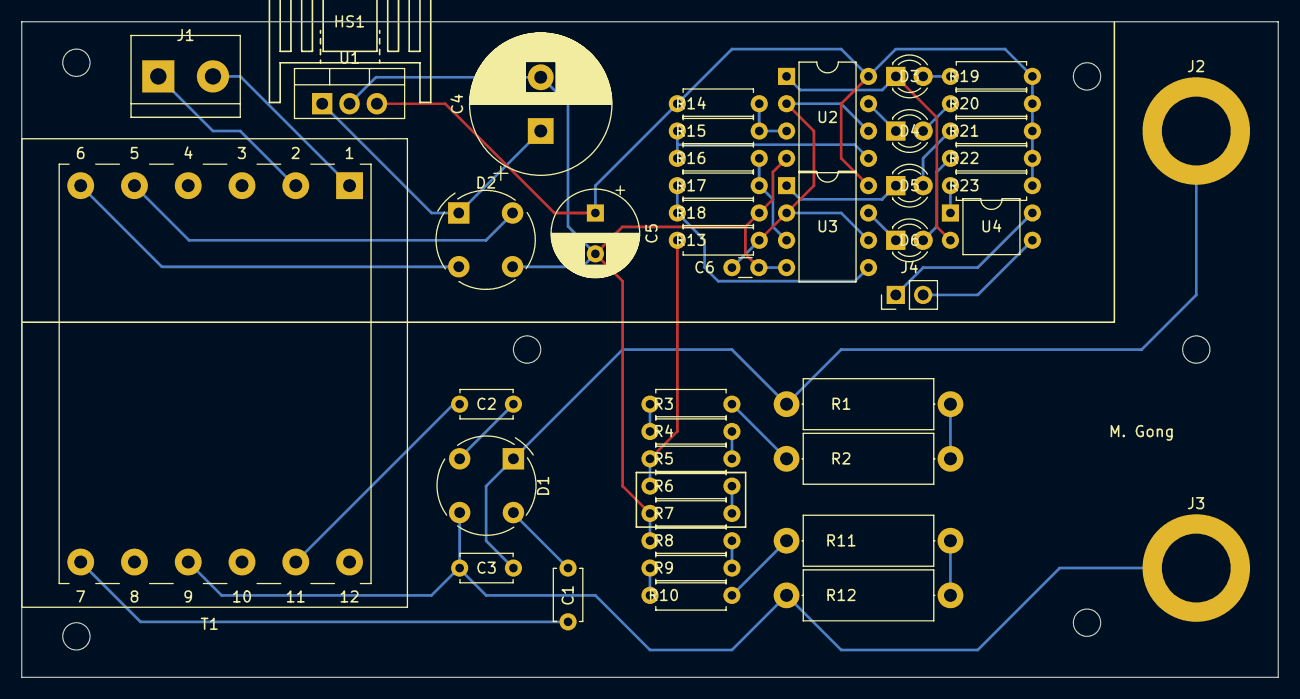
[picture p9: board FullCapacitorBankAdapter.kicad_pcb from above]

Board: 2 copper layers, 116.8 x 61.0 mm, 45 parts (0 on the bottom side), 39 nets.

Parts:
C1, C2, C3: 1nF/1kV; C_Disc_D4.7mm_W2.5mm_P5.00mm
C4: 2200uF; CP_Radial_D13.0mm_P5.00mm
C5: 0.1uF; CP_Radial_D8.0mm_P3.80mm
C6: 0.1uF; C_Disc_D3.0mm_W1.6mm_P2.50mm
D1, D2: 2W10; Diode_Bridge_Round_D9.0mm
D3, D4, D5, D6: LED; LED_D3.0mm_FlatTop
HS1: Heatsink; Heatsink_TO220_15x10mm
J1: AC Power In; TerminalBlock_bornier-2_P5.08mm
J2: Output+; MountingHole_6.4mm_M6_ISO14580_Pad
J3: Output-; MountingHole_6.4mm_M6_ISO14580_Pad
J4: To Control; PinHeader_1x02_P2.54mm_Vertical
R1, R2, R11, R12: 1M 1W; R_Axial_DIN0414_L11.9mm_D4.5mm_P15.24mm_Horizontal
R3, R10: 300K; R_Axial_DIN0207_L6.3mm_D2.5mm_P7.62mm_Horizontal
R4, R5, R8, R9: 220K; R_Axial_DIN0207_L6.3mm_D2.5mm_P7.62mm_Horizontal
R6, R7, R14: 20K; R_Axial_DIN0207_L6.3mm_D2.5mm_P7.62mm_Horizontal
R13, R23: 1K; R_Axial_DIN0207_L6.3mm_D2.5mm_P7.62mm_Horizontal
R15, R16, R17, R18: 4.7K; R_Axial_DIN0207_L6.3mm_D2.5mm_P7.62mm_Horizontal
R19, R20, R21, R22: 2.2K; R_Axial_DIN0207_L6.3mm_D2.5mm_P7.62mm_Horizontal
T1: 6:6:33+33; Transformer_Generic_EE42_12Pin
U1: L7812; TO-220-3_Vertical
U2, U3: LM393; DIP-8_W7.62mm
U4: PC817; DIP-4_W7.62mm

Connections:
+12V: C5.1, R14.2, R19.1, R20.1, R21.1, R22.1, R23.2, U1.3, U2.8, U3.8
/ControlGND: J4.2, U4.3
/ControlSignal: J4.1, U4.4
/PowerIn+: J1.2, T1.1
/PowerIn-: J1.1, T1.2
/PowerOut+: C3.1, D1.1, J2.1, R1.1
/PowerOut-: C3.2, D1.3, J3.1, R12.2, T1.9
GND: C4.2, C5.2, C6.2, D2.3, R7.2, R8.1, R18.1, U1.2, U2.4, U3.4
unnamed: C1.1, D1.4
unnamed: C1.2, T1.7
unnamed: C2.1, D1.2
unnamed: C2.2, T1.11
unnamed: C4.1, D2.1, U1.1
unnamed: C6.1, R13.1, U2.2, U2.6, U3.2, U3.6
unnamed: D2.2, T1.6
unnamed: D2.4, T1.5
unnamed: D3.1, U2.1, U4.2
unnamed: D3.2, R19.2
unnamed: D4.1, U2.7
unnamed: D4.2, R20.2
unnamed: D5.1, U3.1
unnamed: D5.2, R21.2
unnamed: D6.1, U3.7
unnamed: D6.2, R22.2
unnamed: R1.2, R2.1
unnamed: R2.2, R3.1
unnamed: R3.2, R4.1
unnamed: R4.2, R5.1
unnamed: R6.2, R7.1
unnamed: R8.2, R9.1
unnamed: R9.2, R10.1
unnamed: R10.2, R11.1
unnamed: R11.2, R12.1
unnamed: R5.2, R6.1, R13.2
unnamed: R14.1, R15.2, U2.3
unnamed: R15.1, R16.2, U2.5
unnamed: R16.1, R17.2, U3.3
unnamed: R17.1, R18.2, U3.5
unnamed: R23.1, U4.1

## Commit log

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2020-10-09 [Circuit] Add customized footprint and symbol for transformers
    [Power.kicad_pcb, Power.sch]
2020-10-09 [Circuit] Use MOSFETs instead of TRIACs to control the powers
    [Power.kicad_pcb, Power.sch]
2020-10-09 [Circuit] More accurate on the dimension of transformers
    [Power.kicad_pcb, Power.sch]
2020-10-09 [Circuit] Move the Nozzle's MOSFET to power module
    [MPD.sch, Nozzle.sch, Power.kicad_pcb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]
2020-10-09 [Circuit] Add a 1-stage Cockcroft–Walton generator to power module
    [MPD.sch, Power.kicad_pcb, Power.sch]
2020-10-09 [Circuit] Change the isolation transformer to a toroid one
    [Power.kicad_pcb, Power.sch]
2020-10-09 [Circuit] Use a single 12V power for control module
    [Control.kicad_pcb, Control.sch, ControlTester.kicad_pcb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]
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2020-10-09 [Circuit] Move transformers from Power to other circuit diagrams
    [Control.sch, MPD.sch, MiniBleeder.sch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]
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2020-10-09 [Circuit] Add propellant injector into the overall circuit
    [MPD.sch]
2020-10-09 [Circuit] Add a tester board for power switch
    [SwitchTester.kicad_pcb, SwitchTester.sch]
2020-10-09 [Doc] Add details and diagrams to design document
    [MPD.sch]
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2020-10-09 [Circuit] Add a separated battery for Control module
    [CapacitorBank.sch, Control.kicad_pcb, Control.sch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]
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2020-10-09 [Circuit] Separate voltage sensing part into its own schematic
    [CapacitorBank.sch, FullCapacitorBank.kicad_pcb, FullCapacitorBank.sch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]
2020-10-09 [Circuit] Refactor on capacitor bank schematic
    1. Move voltage divider to capacitor bank schematic
    2. Merge mini and full voltage sensing schematics
    3. Add voltage followers
    [CapacitorBank.sch, FullCapacitorBank.kicad_pcb, FullCapacitorBank.sch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]
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2020-10-09 [Circuit] Update the numbers in capacitor bank subsystem
    [CapacitorBank.sch, Converter.kicad_pcb, Converter.sch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]
2020-10-09 [Circuit] Add mini converter module for mini capacitor bank
    [Converter.sch, MiniConverter.kicad_pcb, MiniConverter.sch]
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2020-10-09 [Circuit] Improve the mini converter a little bit
    [MiniConverter.kicad_pcb, MiniConverter.sch]
2020-10-09 [Circuit] Use full bridge rectifier instead of center tapped rectifier in starter
    [Starter.kicad_pcb, Starter.sch]
2020-10-09 [Circuit] Optimize the layout of PCBs of capacitor banks
    [FullCapacitorBank.kicad_pcb, MiniCapacitorBank.kicad_pcb]
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2020-10-09 [Circuit] Merge capacitor bank, converter, and bleeder circuits into one
    [CapacitorBank.sch, Control.kicad_pcb, Control.sch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]
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2020-10-09 [Circuit] Add a PCB design of ZVS module
    [ZVS.kicad_pcb, ZVS.sch]
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2020-10-09 [Circuit] Move the flyback diode from nozzle to switch module
    [Nozzle.sch, Switch.kicad_pcb, Switch.sch]
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2020-10-09 [Circuit] Major redesign on the switch module using self-powered solid state relay
    [Relay.kicad_pcb, Relay.sch, Switch.kicad_pcb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]
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2020-10-09 [Circuit] Fix the direction of diode in starter
    [Starter.kicad_pcb, Starter.sch]
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2020-10-09 [Circuit] Shorten the lines in switch module diagram
    [FullCapacitorBank.sch, Power.sch, Switch.sch]
2020-10-09 [Circuit] Fix the connections around triac
    [FullCapacitorBank.kicad_pcb, FullCapacitorBank.sch, MiniCapacitorBank.kicad_pcb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]
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2020-10-09 [Circuit] Update the control test module to use on the new control module
    [ControlTester.kicad_pcb, ControlTester.sch, Switch.sch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]
2020-10-09 [Circuit] Optimize the interface between capacitor bank modules and voltage sensing module
    [CapacitorBank.sch, ControlTester.kicad_pcb, ControlTester.sch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]
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2020-10-09 [Circuit] Change the interface between control module, switch module, and discharge signal
    [CapacitorBank.sch, Control.kicad_pcb, Control.sch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]
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2020-10-09 [Circuit] Fix a couple issues
    [Control.sch, ZVS.sch]
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2020-10-09 [Circuit] Fix the resistors in voltage sensing module
    [VoltageSensing.kicad_pcb, VoltageSensing.sch]
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2020-10-09 [Circuit] Update the control tester to reflect the changes of control module
    [Control.kicad_pcb, ControlTester.kicad_pcb, ControlTester.sch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]
2020-10-09 [Circuit] Merge voltage sensing into full capacitor bank to form a adapter module
    [CapacitorBank.sch, Control.kicad_pcb, FullCapacitorBank.kicad_pcb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]
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2020-10-09 [Circuit] Use M6 bolt as the connectors of capacitor bank and starter
    [CapacitorBank.sch, FullCapacitorBank.kicad_pcb, FullCapacitorBank.sch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]
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2020-10-09 [Model] Simplify the model of nozzle case, and add a pvc version of it
    [NozzleCase-PVC.blend, NozzleCase.blend]
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2020-10-09 [Doc] Change the full voltage of mini capacitor bank to 50V, and add calculations of energy in capacitors [Circuit] Adjust a resistor to make it lit the top LED at ~50V
    [VoltageSensing.kicad_pcb, VoltageSensing.sch]
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2020-10-10 [Doc] [Circuit] Restore the full voltage of mini capacitor bank to 68V
    [MiniCapacitorBank.kicad_pcb, MiniCapacitorBank.sch, VoltageSensing.kicad_pcb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]
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2020-10-19 [Circuit][Doc] Make the control module triggered by falling edge of the signal
    [Control.kicad_pcb, Control.sch]
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2020-10-21 [Circuit] Use 2 ZVS drivers to drive starter and capacitor bank, instead of switching the coils
    [Power.sch, Switch.kicad_pcb, Switch.sch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]
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2020-10-25 [Circuit] Remove the flyback diode from switch module so the PCB can be smaller
    [Switch.kicad_pcb, Switch.sch]
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2020-10-27 [Circuit][Doc] Correct the voltage calculation in full capacitor bank adapter
    [FullCapacitorBankAdapter.kicad_pcb, FullCapacitorBankAdapter.sch]
2020-10-27 [Circuit] Fix the symbol of DC motor
    [PropellantInjector.sch]
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2020-11-21 [Circuit] Use 2 big capacitors to replace 5 small ones
    [Nozzle.kicad_pcb, Nozzle.sch]
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2020-12-04 [Circuit] Change the track width of nozzle module and switch module to allow larger current
    [Nozzle.kicad_pcb, Nozzle.sch, Switch.kicad_pcb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]
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2021-01-26 [Circuit] Remove the full bridge from the output side of the starter, then change the capacitor bank to non-polarized configuration
    [FullCapacitorBank.kicad_pcb, FullCapacitorBank.sch, MiniCapacitorBank.sch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]
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2021-05-22 [Circuit] Fix the reference of a resistor in starter module
    [Starter.kicad_pcb, Starter.sch]
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
